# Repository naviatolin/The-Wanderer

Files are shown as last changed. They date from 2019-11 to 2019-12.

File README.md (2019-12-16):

# The-Wanderer
Principles of Engineering (POE) Final Project

Electronics-CAD has the electrical schematic using Kicad
Firmware has the Arduino and Raspberry Pi code
Computer_Vision has the computer vision code used by the main Raspi code
The_Wanderer_Website has the website code using Hugo
CAD has the mechnical design files using Solidworks

Within the Firmware folder, i2c_demo is the Raspi code and wheelrun is the Arduino code

See the video of the robot here: https://youtu.be/TBcPSCrN2iE
See the website here: http://poe.olin.edu/2019/wanderer/

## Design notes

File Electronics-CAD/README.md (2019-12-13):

Add the .lib files in this folder to Kicad
Poe_Elias.lib includes an Arduino Uno symbol from a different classmate
Raspberry_Pi_2_3.lib is from https://github.com/lukaneco/Raspberry-Pi-3-library-for-kicad but their part is not actually used.
There are other parts saved to that library folder such as Raspberry_Pi_3 that Case modified existing parts for.

Run The-Wanderer.sch in Kicad to edit the schematic.

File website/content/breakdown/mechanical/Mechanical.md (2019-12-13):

---
title: 'Mechanical Breakdown'
---

There are two main components to the mechanical design: the legs and the chassis. We chose a four-bar linkage mechanism for the legs because it gave the tottering movement we wanted without being too complicated. The leg mechanism uses one continuous rotation servo for each side, giving a total of two.

<!--more-->
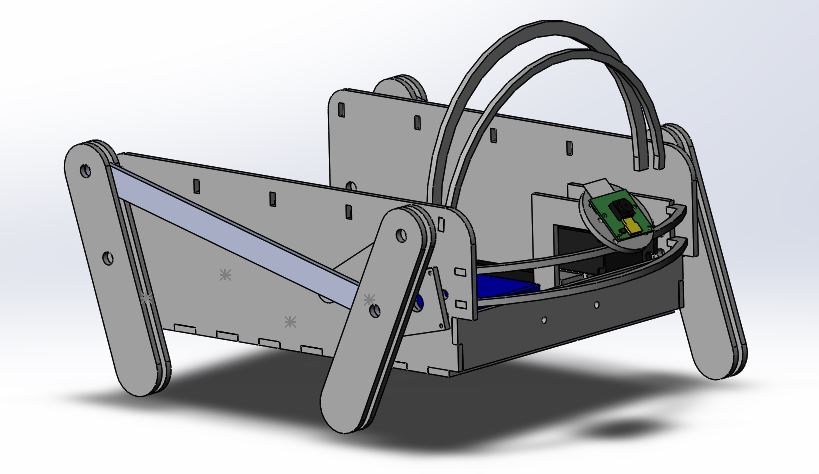
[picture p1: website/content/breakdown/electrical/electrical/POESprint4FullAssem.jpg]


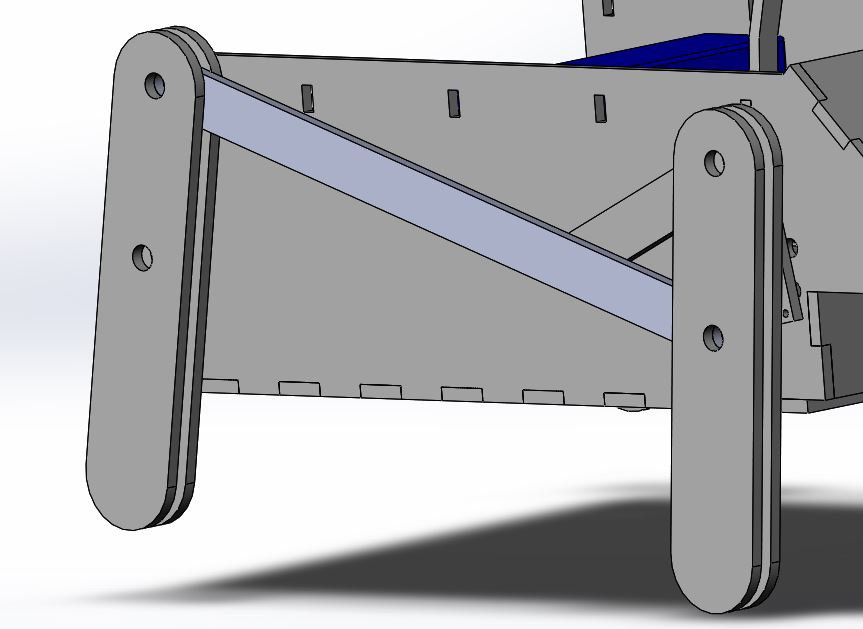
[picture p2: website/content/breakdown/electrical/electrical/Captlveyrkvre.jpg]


We used a four-bar linkage mechanism we found online ([https://grabcad.com/library/walking-robot-mechanism-1](https://grabcad.com/library/walking-robot-mechanism-1)) and adapted it to meet our design criteria. The main alterations we made to the design were scaling it up and increasing its robustness. We increased robustness by thickening the members and doubling them up where we needed more traction with the ground. We scaled up the design to fit our electronics while maintaining the size ratios between the linkages. We used the longest connector piece as our reference since it was the closest approximation to the chassis length and then scaled all the other parts of the linkage by the same factor. The legs are fabricated out of laser-cut fiberboard because it was lightweight and in abundance around our work-space.

Parallel to the mechanical design is integrating the mechanical and electrical systems together. The size of the Wanderer is mostly determined by the space needed for internal electronics and wire routing. The arrangement of the internal electronics ensures that each component can function and the software team can connect to the Raspberry Pi and Arduino for programming.

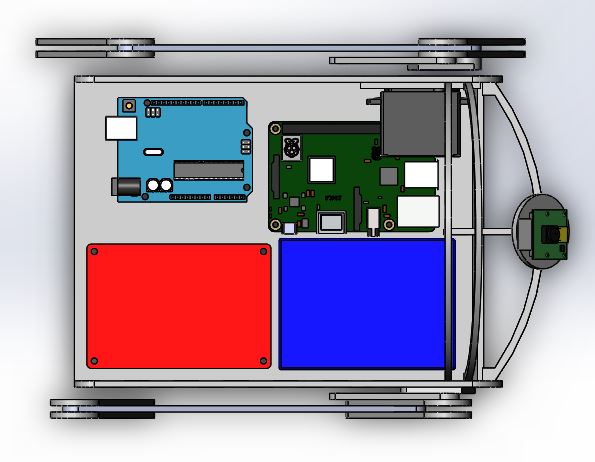
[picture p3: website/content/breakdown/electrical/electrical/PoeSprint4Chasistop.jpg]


One of the main goals of our project was to make our robot cute. One of the biggest things we did to accomplish this was the design of its motion and the use of the leg four bar linkage, Another large part was the overall aesthetic design of the chassis. One of our biggest aesthetic design features in the bright fuchsia fur we used as a skin for our robot. In order to accommodate this and improve the overall shape of the chassis, we added a set of ribs to the top of our robot: 5 uniformly spaced and one slightly smaller and tilted forward at the front, and a set of two much smaller ribs on the front. With the fur stretched over them, they gave the robot a cute animal-like shape. 

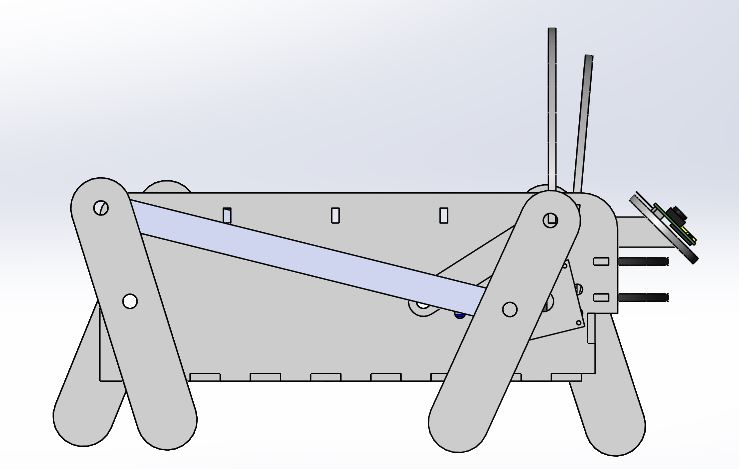
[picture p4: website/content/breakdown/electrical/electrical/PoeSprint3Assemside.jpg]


In order to maintain cuteness we also needed to disguise our sensors. We hid the camera as part of the robot's nose design. We mounted it at a 45 degree angle on a stalk that connected to the bottom of the chassis and such out of the robot just above the front ribs. We hid the IR sensor by mounting it slightly inset at the bottom of the front of the robot so that it would not be visible from above.  

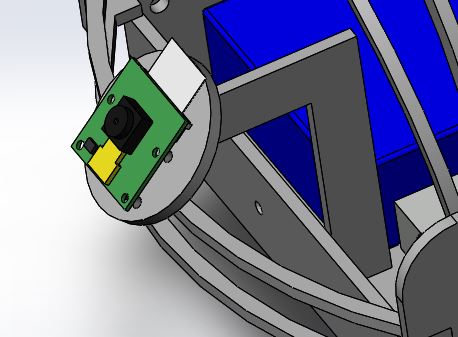
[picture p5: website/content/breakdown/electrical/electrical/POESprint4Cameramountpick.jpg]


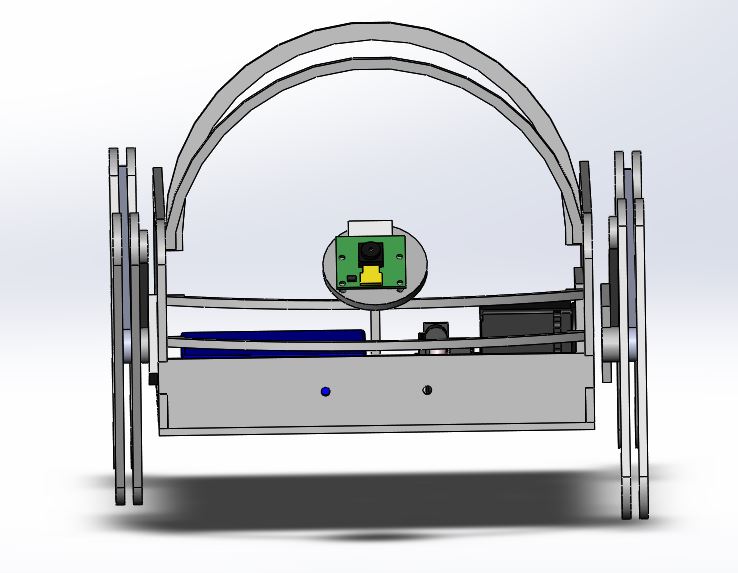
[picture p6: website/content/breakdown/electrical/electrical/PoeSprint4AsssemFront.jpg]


When it came to final assembly, the large laser-cut pieces were clamped and wood glued, then the smaller pieces were superglued. Any holes for mounting electrical components had press fit threaded inserts, allowing for easier installation than nut and bolt fastening. The leg mechanism to servo connection required one 3D printed piece, and the rest of the leg mechanism was fastened with plastic shafts and spacers.

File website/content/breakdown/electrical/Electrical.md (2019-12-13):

---
title: 'Electrical Breakdown'
---
For the electrical design, the biggest step was converting 12V battery power to 5V for the Raspberry Pi and servo motors. Two voltage dividers were needed to allow signal capture while preventing pin damage. The rest of the electrical was connecting components so that the software team has everything they need to program the robot behavior. The schematic for the electrical design is below, and subsystem descriptions follow.

<!--more-->

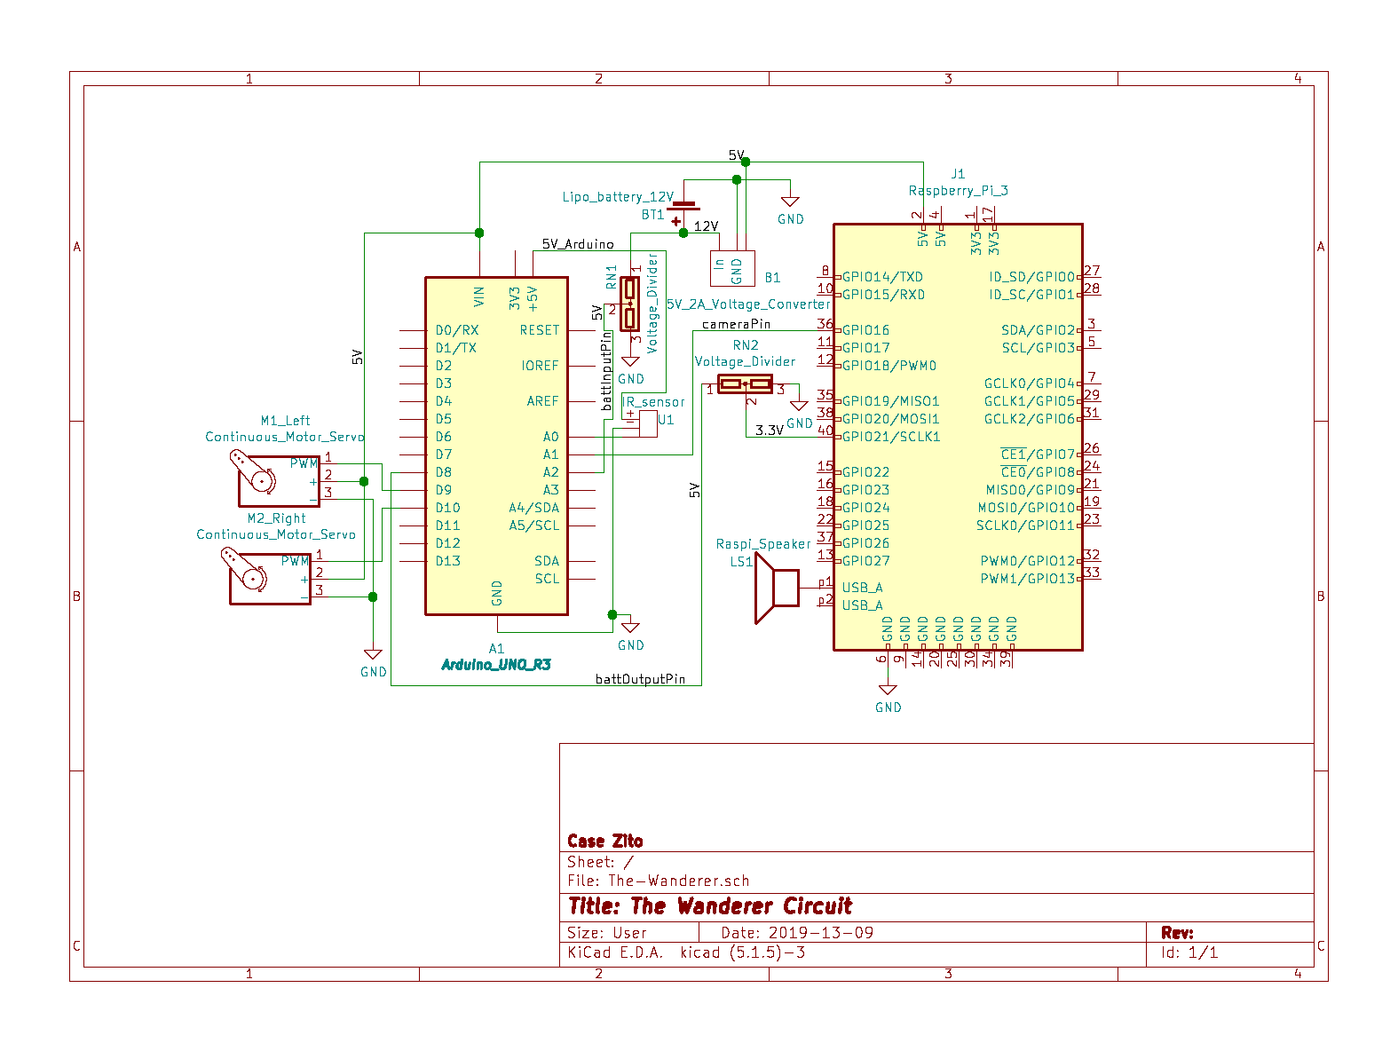
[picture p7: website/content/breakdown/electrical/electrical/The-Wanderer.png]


## Power Conversion:

- The 12V battery directly powers the Arduino while the Raspberry Pi and Servos require 5V with significant current. We used 4 5V 0.5A voltage converters in parallel to provide ample power. We chose these components because they were readily accessible and simple to implement; providing 12V and ground, these ICs output 0.5A at 5V with proper heat dissipation. We needed to supply at least 1A of current to the Raspberry Pi to keep up with sustained peak load while processing images, so we doubled the power capacity of the conversion circuit to accommodate any future components, which turned out to be the servos. A simpler thing would be to use a 5V 2A voltage converter (linked in our bill of materials).

## Voltage Dividers:

- Battery monitoring by Arduino- To prevent overdraw of the battery, we want the system to measure the level of the battery. With a range of 10.8-12.6V, the Arduino cannot natively sample the battery level, so we constructed a voltage divider with a scale factor of 0.231, placing the measured battery level in the 2.5-3.0V range. The resistor values used for this divider are 9k and 30k, where 9k/(9k+30k) = 0.231.
- Low battery signal from Arduino to Raspberry Pi- The Raspberry Pi and Arduino have differing logic levels of 5V and 3.3V, respectively. For the Arduino to indicate a low battery, its 5V digital signal must drop to 3.3V. Since this connection is only one way, we used a voltage divider with a scale factor of 0.66. The resistor values used for this were 10k and 20k, giving 10k/(10k+20k) = 0.66.

## Arduino Pins:

Arduino directly powered by the battery through the barrel jack

- A0- connected to the output of the infrared sensor
- A1- connected to the Raspi pin 36, the cameraPin
- A2- measures the battery level through a voltage divider, the battInputPin
- D8- sends the "low battery signal" to the Arduino through a voltage divider input, battOutputPin
- D9- PWM signal for the left servo motor
- D10- PWM for the right servo motor

## Raspberry Pi Pins:

Raspberry Pi powered by the 5V2A converter on pins 4 and 6.

- GPIO16 (pin 36)- sends person detection indication to Arduino (cameraPin)
- GPIO21 (pin 40)- receives low battery indication from Arduino through a voltage divider
- USB- USB speaker for sounds
- Note: In order to program the Raspberry Pi, we used a wireless mouse and keyboard and then plugged a monitor into the HDMI

## Other Components:

- The IR sensor is powered and monitored by the Arduino
- The servos are powered by the 5V2A converter and controlled by the Arduino's PWMs

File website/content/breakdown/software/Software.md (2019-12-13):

---
title: 'Software Breakdown'
---

Github: [https://github.com/naviatolin/The-Wanderer](https://github.com/naviatolin/The-Wanderer)
<!--more-->

### Communication between Raspberry Pi and Arduino

Initially, we were going to use some form of serial communication to exchange information between the Raspberry Pi and Arduino. We successfully prototyped this but eventually scrapped it in favor of simple digital pin indicators, even though this meant some extra hardware. The Raspberry Pi sends a digital signal to the Arduino to indicate the presence of a person, at which point the Arduino stops the motors. The Raspberry Pi is 3.3V logic level, so the Arduino measures this digital signal on an analog pin. In the final product, we set the Arduino to test the battery level and relay whether it is below a set level or not to the Raspberry Pi via a digital pin. 

### Arduino "Wheelrun" Code

The Arduino's main function is to control the movement of the robot. The proxPin reads analog voltage from the IR sensor and at a certain threshold the code has the robot turn (one wheel going forward, the other backward) in order to avoid obstacles. The Arduino also monitors the battery level through the battInputPin and converts the signal to a High or Low out of the battOutputPin to communicate low battery to the Raspi. From the Raspi, the cameraPin tells the Arduino to stop when the Raspi sees a person.

### Raspberry Pi "I2C_demo" Code

For part of our prototyping process, we explored having the Raspberry Pi and Arduino communicate with I2C. Although we used digital pins in the end, we did successfully exchange information between them using I2C. In I2C_demo we have the Raspberry Pi look for people through the Raspi camera, then tell the Arduino if it sees them through the pin 36. The Raspi also handles the speaker for the robot. If it receives a low battery signal from the Arduino through pin 40, it outputs a "low battery" sound. When the camera sees a person it outputs a "hello" noise and after 8 seconds, roughly the time it takes to process that a person would no longer be there, it outputs a "goodbye" noise.

### Computer Vision Code

Using OpenCV for Python, we used an implementation of the YOLO-COCO algorithm from a previous software project. This is the most computationally intense part of the project and is why we added the Raspberry Pi to the Wanderer. YOLO-COCO breaks in image down into an array of variously sized pieces (called a blob) and treats each with a large (300MB) weights file to detect a wide range of objects. To minimize computation time and increase robot responsiveness, we reduced the blob size to a minimum, sacrificing some detection ability. In the future, we would probably switch to a more specialized version of YOLO-COCO to reduce computational load.

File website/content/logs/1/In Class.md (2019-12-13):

---
Title: Oct 18, 2019
weight: 1
---
<!--more-->
## Goals

- Get started on the individual tasks that we have assigned.

## What Did We Get Done

- decided on walking mechanism - wheels for
- case: wheels running
- how the legs will incorporate
- chassis cad
- started on circuit schematic related things
- opencv testing

## Teaching team feedback

- Adding an axis of movement increases difficulty by a lot
- Having legs that move is much more difficult than wheels, so may have to go back to wheels
- Make sure the software can do what we want it to early, because if we run into issues with computer vision it will halt progress in our project
- Sensing is a difficult part, especially for connecting the sensing to the computer vision

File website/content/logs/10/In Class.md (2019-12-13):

---
Title: Nov 15, 2019
weight: 10
---
<!--more-->
## Goals

- raspi arduino communication
- put holes in the cad
- get the crank cad started
- block diagram

## What Did We Get Done

- block diagram



- we have successfully communicated whether or not we see people between the arduino and the raspberry pi
- started the crank cad
- holes in the cad

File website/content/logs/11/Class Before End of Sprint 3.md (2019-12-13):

---
Title: Nov 19, 2019
weight: 10
---
<!--more-->
## Class Before End of Sprint 3

On the mechanical side, the robot was completely assembled by Anna and Michael on Sunday. Case  uploaded the Arduino code to the robot and modified to work for the new Servo motors. One leg was not working correctly, and from Case and Michael trouble shooting it became apparent that it was a mechanical issue.

## Goals

During today's class, we focused on fixing the mechanical issues with the legs. Anna and Michael worked on adding spacers and loosening joints for the legs so they would have less friction and be able to move. Navi and Case had finished their respective parts of the code, Raspi writing to digital pins when it sees a person or is talking, and the Arduino running the motors and deciding when to stop (based on Raspi) or turn. We had the goals to upload speaker sounds to robot and to look at requirements of the website.

## What Did We Get Done

We fixed the mechanical issues and then tested the Arduino movement code. We fixed up the movement so that it successfully moves forward and turns. We also found that we will be prepared to upload to the robot because we can convert Notion pages to markdown or html. Tomorrow we will upload speaker sounds to robot.

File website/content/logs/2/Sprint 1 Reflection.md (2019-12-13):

---
Title: Oct 25, 2019
weight: 2
---
<!--more-->
## Sprint 1 Reflection

## Plusses

### Navi

- We worked really well together on gettting things done and had great communication
- Came up with clear implementation plans very quickly
- Ideated well
- We vibed

### Michael

- Mental Health transparency
- Lots of CV work ported over from SP19
- Communication
- Lots done in class
- Progress updates

### Case

- good communication
- good product, i feel accomplished
- we're sticking to our goals and routines well
- felt listened to in meetings
- got everything we wanted to done!

### Anna

- good team dynamic
- productive meetings
- good communication
- I like our project
- well scoped

## Deltas

### Case

- Did the assembly kinda last minute
- lasercutting was also a bit last minute, and if we had to make serious changes to the CAD the schedule would have gotten messed up (do earlier separate CAD? have a more set idea of things early? idk)
- not always sure what's happening with subtasks before i ask- clear progress checks about specific tasks is good moving forward into more complicated things
- uneven writing and tracking of tasks (team captain for a meeting)
- presentation was a little rocky, practice more

### Navi

- documentation and website/blog as this is our final deliverable
    - i could've done a better job as a pm
- need to set up clear tasks and objects every meeting - need to spend 10 minutes just doing stuff like this
- could've practiced presentation
- could've done another iteration as well?
- could've talked more about the personality as a group and had an ideation session
- next sprint should meet more outside of class

### Michael

- Improve aesthetics of robot for sprint 2
- Presentation practice
- Use github more
- Gimme more tasks!

### Anna

- not enough meetings
- Practice presentation/ evenly divide slides
- more involved schedule
- get my cad in github

## Next Sprint

Kaizen: More meetings and more documentation (be more thorough)

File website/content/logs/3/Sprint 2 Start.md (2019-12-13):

---
Title: Oct 27, 2019
weight: 3
---
<!--more-->
## Sprint 2 Start

## Goals

- Assigning tasks for sprint
- Making a sprint calendar
- knowing sprint goals
- start working on sprint tasks
- talk about personality and do some ideation

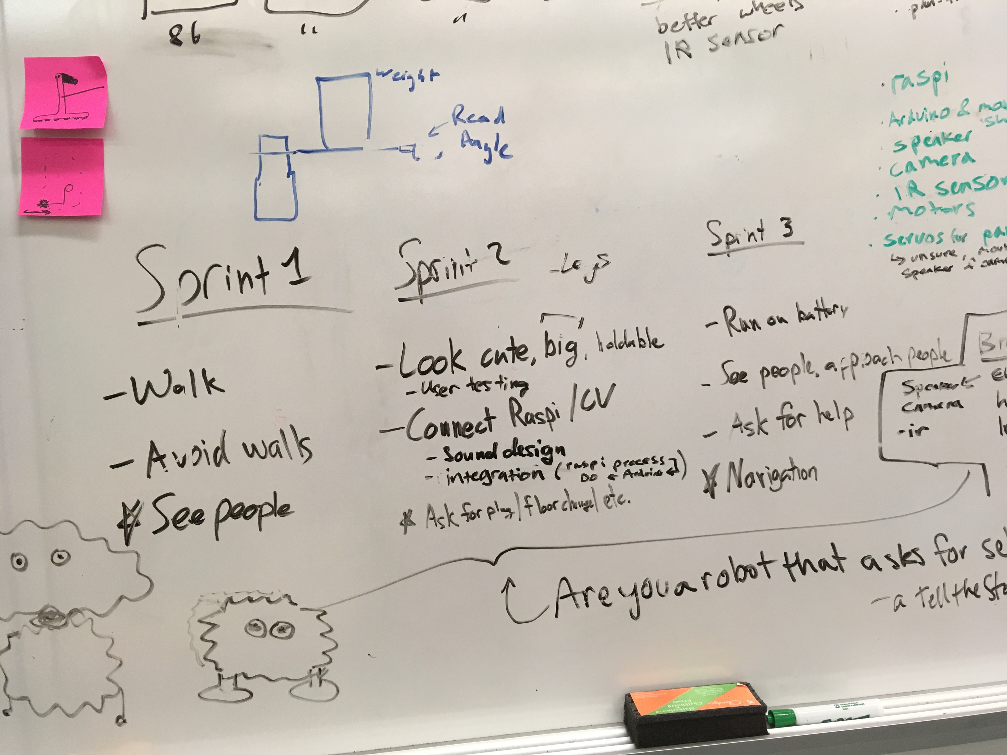
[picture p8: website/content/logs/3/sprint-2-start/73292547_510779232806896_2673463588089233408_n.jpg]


## What Did We Get Done

- we got sprint 1 finished

## Reflection (Where could we improve in the future?)

We decided sprint priorities, scheduled our sprint tasks, and then focused on personality/aesthetic ideation

We want to track time we spend on tasks for sprints

We decided team bonding

we decided on immediate tasks

We were not able to start sprint tasks much

## Priorities for Sprint

- Good mobility → turning, walk forward
- Chassis fits all components, decide all components will be on all of it
- Figure out sensor requirements, what components we will have
    - We decided to do minimum sensors for now, and scale up if needed. This means the head will just have one servo
    - Two DC motors for legs, one IR sensor, Raspi camera, Raspi speaker, Arduino & motor shield, Raspi, servo for head tilt
- Raspi and Arduino communication, proof of concept that we can send commands to Arduino
- Personality/design goals → decide what inspiration we want for design and what thing we want to

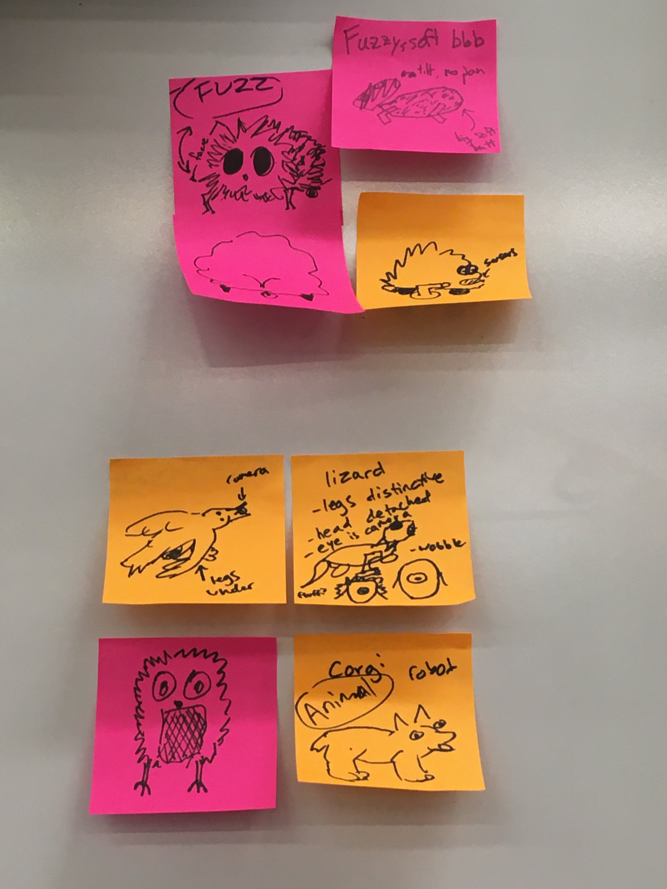
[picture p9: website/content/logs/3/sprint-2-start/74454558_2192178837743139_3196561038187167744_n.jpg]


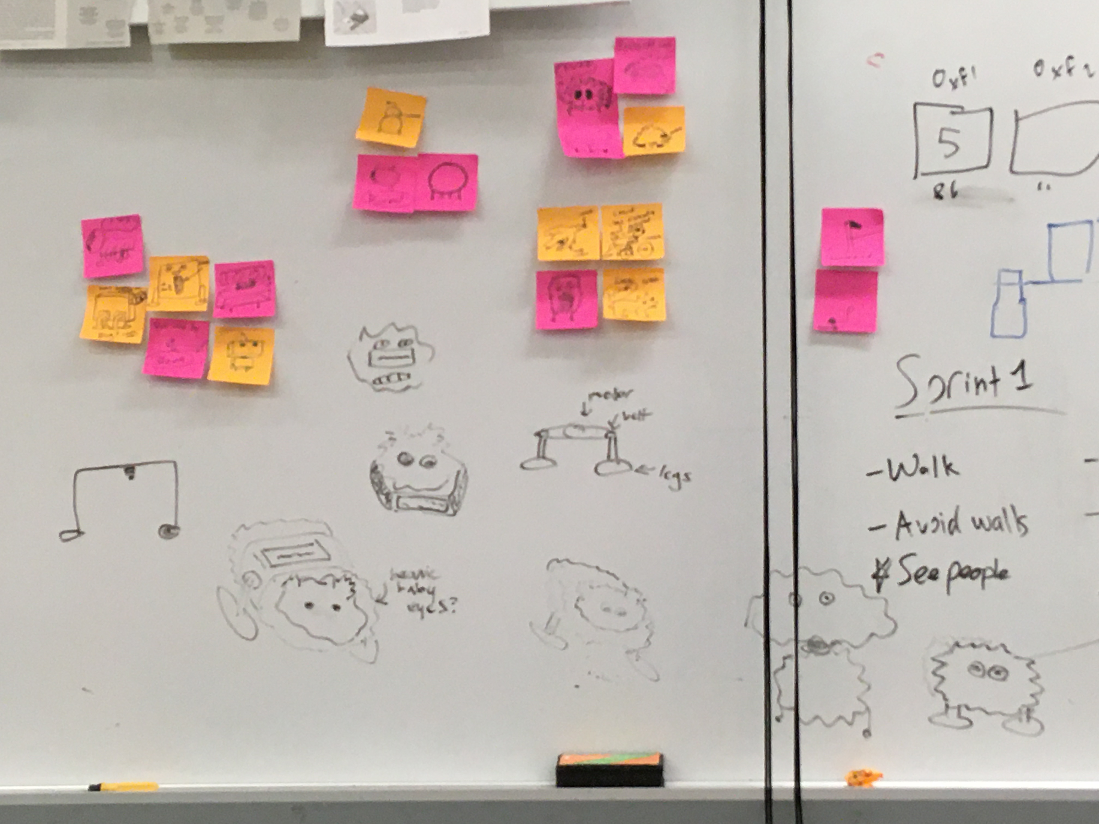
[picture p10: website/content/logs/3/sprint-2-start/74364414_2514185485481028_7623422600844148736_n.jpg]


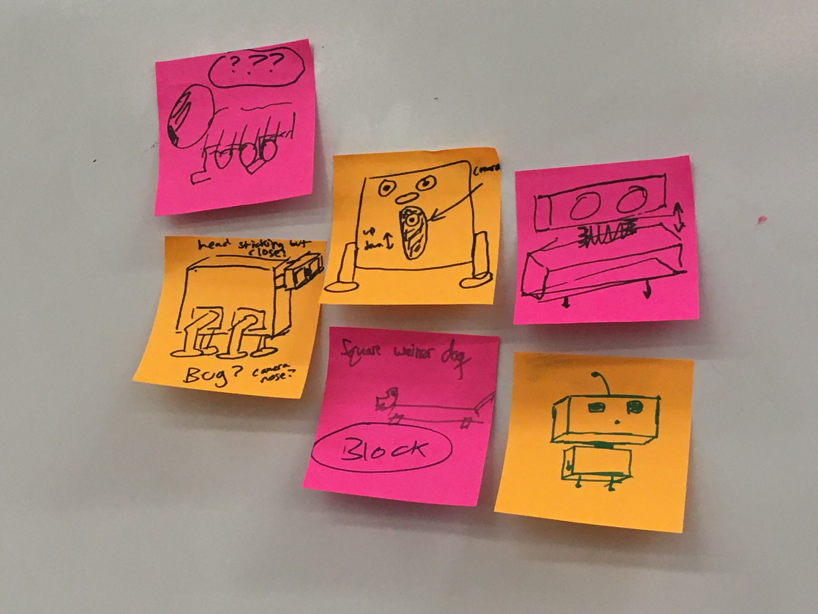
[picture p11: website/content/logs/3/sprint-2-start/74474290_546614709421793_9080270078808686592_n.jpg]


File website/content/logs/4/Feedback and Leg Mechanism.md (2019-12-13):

---
title: Oct 29, 2019
weight: 4
---
<!--more-->
## Feedback and Leg Mechanism

## Goals

- Figure out our feedback
- Finalize the leg mechanism

## What Did We Get Done

- Got the raspberry pi partially set up (getting python 3 and open cv stuff on it)
- stared at leg mechanism
- made progress
- started on getting the website up

## Reflection (Where could we improve in the future?)

- walk into the meeting with clearer goals and realistically estimate the deadlines

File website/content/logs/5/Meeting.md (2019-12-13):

---
title: Nov 01, 2019
weight: 5
---
<!--more-->
## Goals

- Decide what we want for our team bonding
- Tonight: Have dinner, have fun

## What Did We Get Done

- Anna researched wheels
- Navi got first pages of github website showing
- We ran into an error where the raspberry pi crashed every time we tried to run the python code to detect people. We then tried to use Simple CV and other example people got working on their 1GB ram raspberry pis. The raspi continued to crash. :(

## Reflection (Where could we improve in the future?)

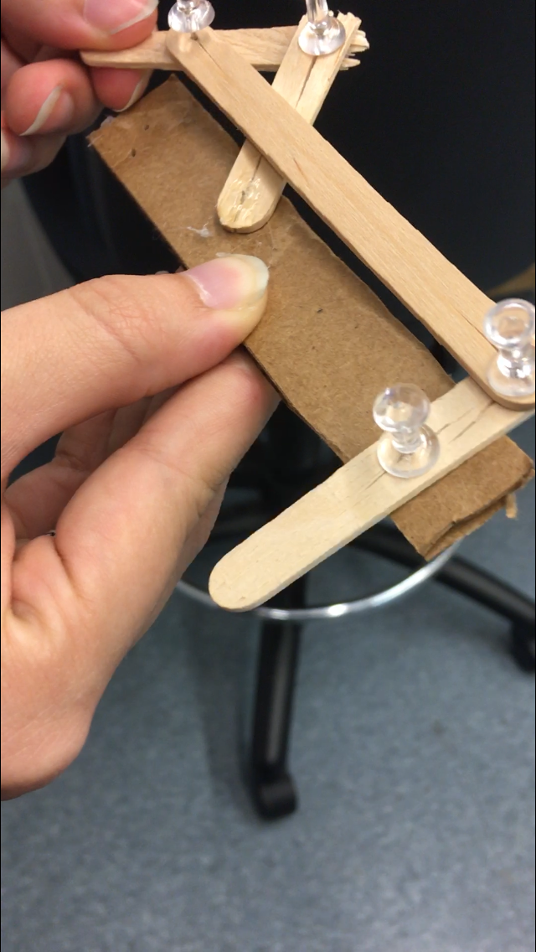
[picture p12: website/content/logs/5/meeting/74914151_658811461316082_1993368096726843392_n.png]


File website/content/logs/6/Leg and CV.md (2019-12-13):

---
Title: Nov 03, 2019
weight: 6
---
<!--more-->
## Leg and CV!

## Goals

- Figure out the rest of the CV situation
- Figure out the chassis and leg situation

## What Did We Get Done

- We fixed the issue with the CV crashing the raspberry pi. We realized that this was due to a power supply issue where the previous brick was only supplying the raspi with 0.7A of current where we really actually needed 2.5 to 3 A of current. This was a big win. We now have proof of concept that the raspberry pi can detect people in it's field of vision.
- With the legs, we finished cadding them and decided on what the chassis would look like for this sprint.
- Yesterday, we went to the thrift store and bought potential skins.



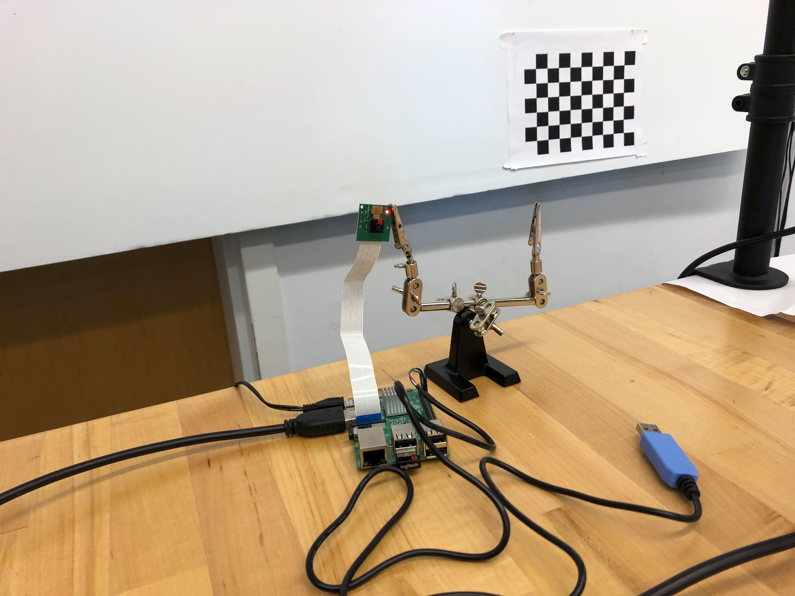
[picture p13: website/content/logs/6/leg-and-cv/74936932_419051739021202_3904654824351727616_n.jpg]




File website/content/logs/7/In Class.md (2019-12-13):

---
Title: Nov 05, 2019
weight: 7
---
<!--more-->
## Goals

- Construct the prototype from lasercut pieces
- Start working on different skins

## What Did We Get Done

- We got the Raspberry pi and the arduino to communication using i2c. The arduino blinks based on information sent to it using the raspi.



- We got some skins for the robot using the children's clothing we thrifted earlier.
- Cadded spacers, made edits to the chassis
- Laser cutting out a box for the chassis as a skin
- next revision will be putting this power supply on a piece of metal
- need a thing that will shut off the robot if the power is overdrawn
- 2 amp 12 v to 5 v converter - the raspberry pi only taked 5v but the arduino can handle 12 but will step it down to 5 volts



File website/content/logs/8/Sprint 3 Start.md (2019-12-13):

---
Title: Nov 10, 2019
weight: 8
---
<!--more-->
## Sprint 3 Start

## Goals

- Look at slide feedback and reflect
- Look at sprint goals and create tasks for the sprint
- decide what things we will buy this week
- Test out prototype and see how it moves
- Integration mechanical goal: making working chassis
- Mechanical mechanical goal: increasing stability of legs, 3D print attachment, order better motors
- Software goals: comp vis to moving something, get speakers to work, get LCD working
- Figure out how to integrate more as a team

## What Did We Get Done

- Set goals for sprint
- planed out tasks for sprint
- decided things to order
- split up tasks for software and made smaller due dates

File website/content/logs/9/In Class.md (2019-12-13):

---
Title: Nov 12, 2019
weight: 9
---
<!--more-->
## Goals

- Mechanical: decide on a chassis design, get cadding
- chat with aaron about stability and weights
- finish figuring out raspi arduino stuff
- brainstorm and try different code

## What Did We Get Done

- Case&Navi: Looked at digital IO on Raspi, played with camera angles (45deg is best), block diagrams/state machine of robot behavior
- Anna & Michael: Sketched out chassis stuff, talked about motor power and structure stability, walks with weights
- Michael: Ordered perfboard for the circuit
- Order sheet: IR sensor, speaker, motor, battery

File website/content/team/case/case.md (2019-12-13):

---
title: 'Caze Zito (He/Them)'
---
<!--more-->
{{< figure src="case.jpg" width="400px">}}

Case is a electrical and computing engineer who also often does software. They really loved doing a lot of Arduino coding for this project, circuit schematic making, and other bits and pieces for this project. It was great to see the fluffy monster that came out of everything.

Github: [https://github.com/CaseZito](https://github.com/CaseZito)

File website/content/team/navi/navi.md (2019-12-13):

---
title: 'Navi Boyalakuntla (She/Her)'
---
<!--more-->
{{< figure src="navi.png" width="400px">}}

Navi is an product design engineer (EECS with Design) at Olin College of Engineering. She enjoyed working on integration between the arduino and the raspberry pi and working on developing the robot's personality. She also took on the role of project manager in this team using tools like agile scrum and Notion.

Github: [https://github.com/naviatolin](https://github.com/naviatolin)

LinkedIn: [https://www.linkedin.com/in/pranavi---boyalakuntla/](https://www.linkedin.com/in/pranavi---boyalakuntla/)

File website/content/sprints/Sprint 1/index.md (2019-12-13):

---
title: 'Sprint 1'
---

## Goals:

- Make a robot that walks around and can sense walls
- Show proof-of-concept for components
    - Computer vision demonstration
    - Walking mechanism

## Progress:

- Robot walks and can sense walls. It is able to turn before the wall
    - Computer vision can recognize people
    - Basic walking mechanism
<!--more-->
## Mechanical

- Create a rectangular chassis to mount motors, wheels, IR sensor, and Arduino
    - There are three wheels, one on front two on back
    - Moves forward with 2 legs driven by motors. The legs spin around with the foot facing downward, dragging it forward
    - Mount IR sensor on the front to sense walls

{{< figure src="sprint1pic1.jpg" width="400px">}}
{{< figure src="first_proto.png" width="400px">}}

## Software

- Code that turns robot before wall, and runs legs

## Design

- Robot wobbles and walks slowly

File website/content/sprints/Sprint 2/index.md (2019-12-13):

---
title: 'Sprint 2'
---
We want to develop the personality of the robot more especially with mechanical design and do a lot of user testing to make sure that the robot is "cute" and personable.

## Goals:
- Implement computer vision on the Raspberry Pi
- Use Raspberry Pi to communicate with Arduino
- Improve walking mechanism
- Develop robot appearance/personality especially making it "cute"

## Progress:
- Moves with improved linkage leg mechanism
- Can identify people with the Raspi camera
- Has fluffy "pink monster" appearance people found cute
- The walking mechanism has a wobble aspect which adds a cute personality factor
- Arduino LED lights up when Raspi sees a person (10 sec)

<!--more-->

## Mechanical

- Have a functional leg mechanism
    - iterations: foot shape, 3D print, longer legs
    - [https://grabcad.com/library/walking-robot-mechanism-1](https://grabcad.com/library/walking-robot-mechanism-1) Decided on 4 leg linkage design based on this

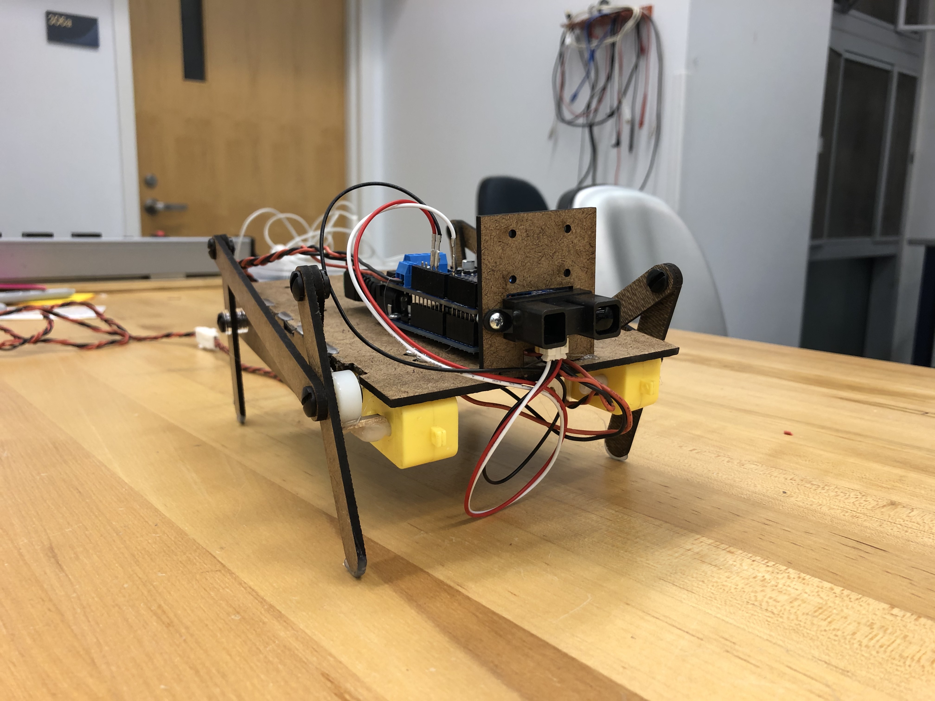
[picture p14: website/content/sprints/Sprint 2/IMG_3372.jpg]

Markdown Monster icon

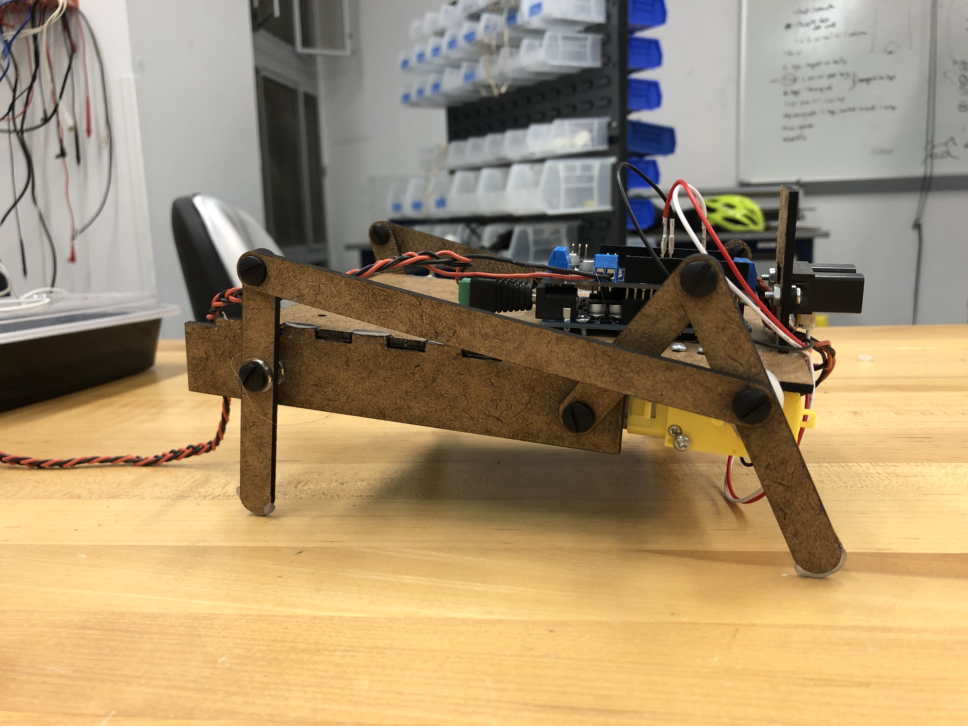
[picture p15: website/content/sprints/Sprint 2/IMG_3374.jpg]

Markdown Monster icon

## Software

- Finalize sensors we want and goals
- Raspberry Pi-Arduino integration

## Design

- Research into types of walk cycles: peppy, confident, meandering, off-balance. We liked the back and forth movement that the linkage produced
- Mock up type of skins. People loved the pink fluff monster skin
    - Furry monster like (pink fluff)
    - Furry animal like (cow print fuzzy)
    - Technical look (see through panel acrylic)
- Discussed type of shape
    - Give it a butt, stuffed look
    - Make it rounder- skin sags in the middle

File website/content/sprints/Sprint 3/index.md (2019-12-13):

---
title: 'Sprint 3'
---
## Goals

- Integrate mechanical electrical and software systems
- Scale up to final size
- Increase mechanical robustness (no hot glue!)
- Run on battery power

## Progress:
- Attached new motor servos
- Added battery and convert its power for other components
- Arduino and Raspi wired to each other on chassis and communicate back and forth, with Arduino controlling movement and the Raspi monitoring computer vision and using the speaker
- Stronger larger design that is wood glued, not hot glued
- Added ribs on chassis over electronics to give round shape to body and fur

<!--more-->

## Mechanical

- Improve walking, by making legs thicker, making a CAD assembly, 3D printing crank part (so its a stronger and spaced right)

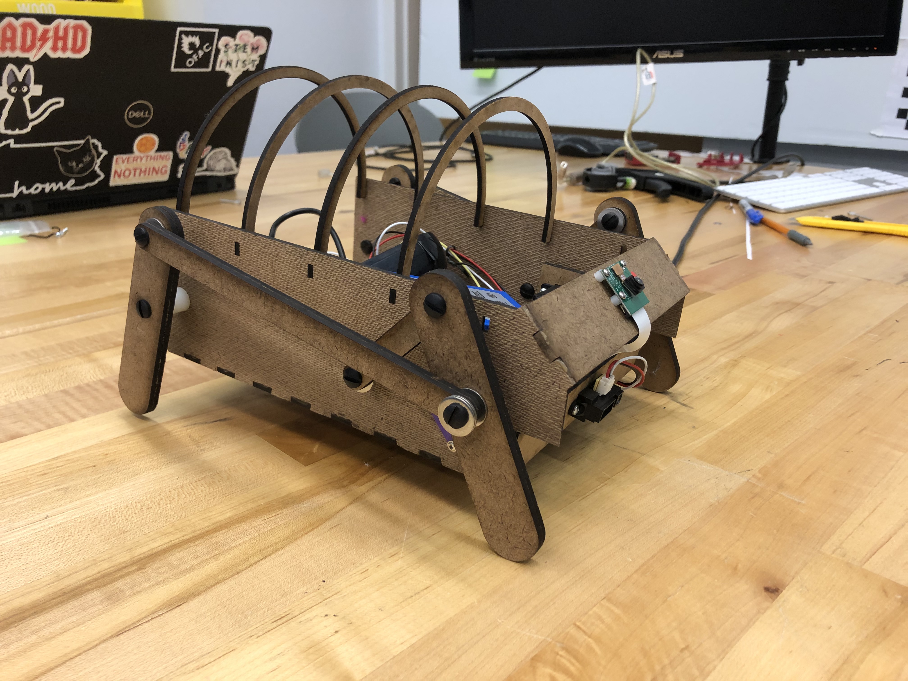
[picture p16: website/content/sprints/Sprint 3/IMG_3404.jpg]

Markdown Monster icon

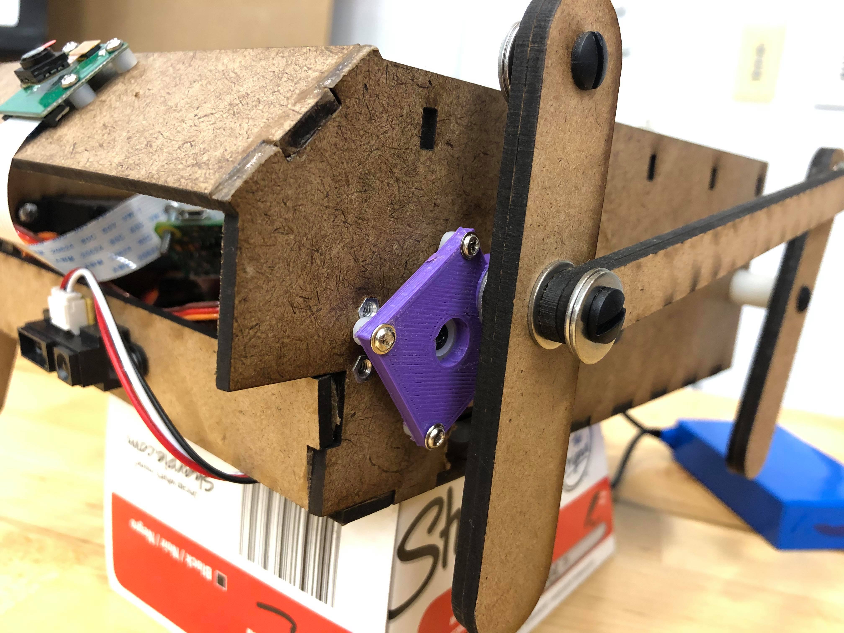
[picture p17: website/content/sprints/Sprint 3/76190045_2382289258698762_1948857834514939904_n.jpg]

Markdown Monster icon

## Electrical

- Move to battery power
- Wiring to connect Raspi, Arduino, battery, and components

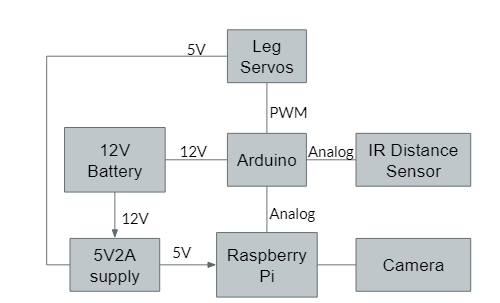
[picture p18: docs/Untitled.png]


## Software

- Add sounds, and change in movement to program interactive behavior
- Add lines of code to .bashrc Raspi file, so that the Raspi runs the computer vision/main code from start-up
- Connect Raspi GPIO pins to Arduino to communicate the "stop" signal when Raspi sees a person and is talking. Arduino should stop moving.

Markdown Monster icon

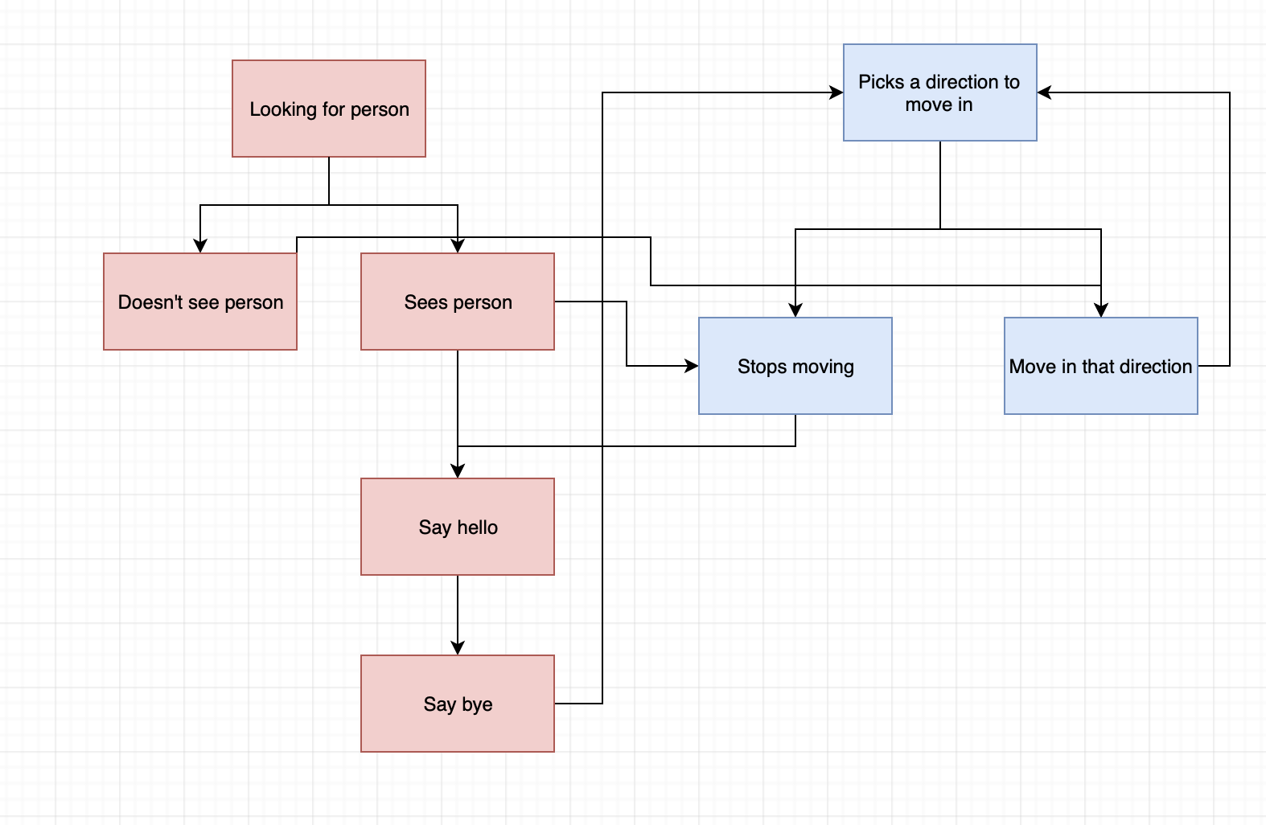
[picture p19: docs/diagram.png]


- Get speaker working and saying one sound (a roar) when it sees a person

## Design

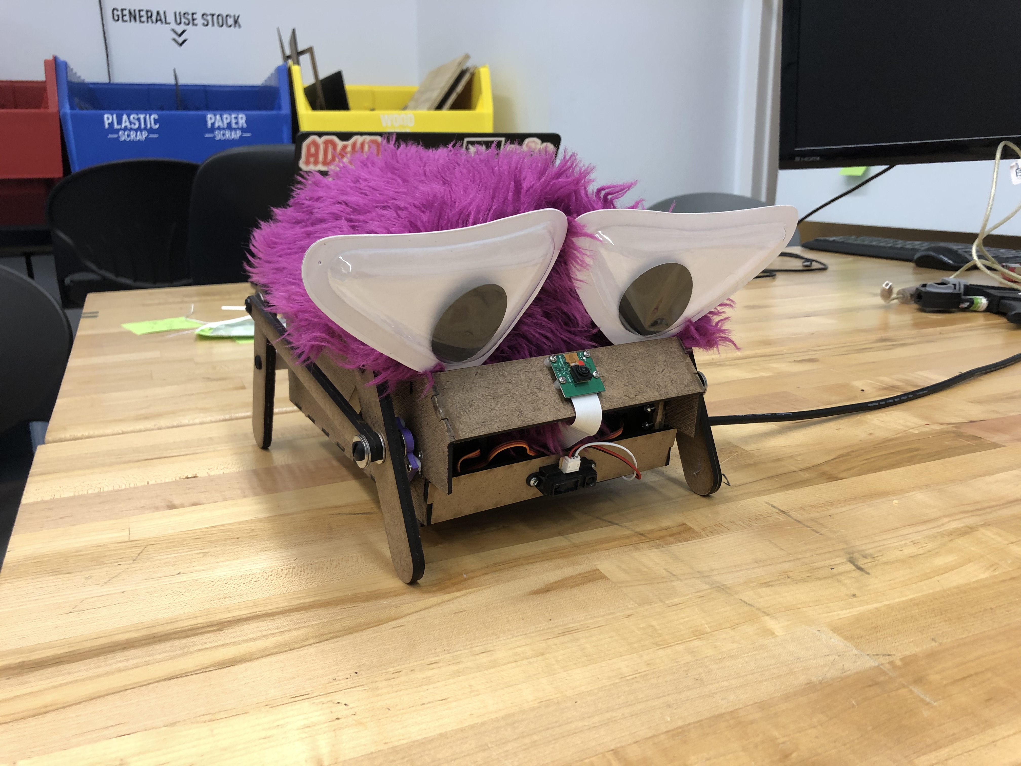
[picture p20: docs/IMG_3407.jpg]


- Iterate on appearance, creating round hardboard ribs to put fur over parts, putting on fur, putting on eyes, making it more chunky (more towards square wall-e and round ideas)

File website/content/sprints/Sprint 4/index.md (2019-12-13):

---
title: 'Sprint 4'
---
## Goals:

- Add low battery notification (over speaker)
- Redesign chassis to organize electronics for better access
- Make shape rounder
- Documentation
- Modify sounds to be more cute

## Progress:

- Added low battery notification sound by having the Arduino sense voltage from Battery, output digital high or low, convert that voltage to 3.3V range for Raspi, and have Raspi output battery low sound
- Added more small ribs to structure give a gradual rounding shape
- Redesigned chassis and had threaded inserts for parts so they held better
- Decided against modified sounds because we liked the attitude of them (very attention getting)
- Finished up Documentation
<!--more-->
## Mechanical

- Redesign chassis so that components are easier to access
- Chassis has round, semi-circle design, with ribs in the front instead of hardboard to add a round face
- Create a hardboard protrusion with a circle to come out of the fur as a fake "nose" that has the camera

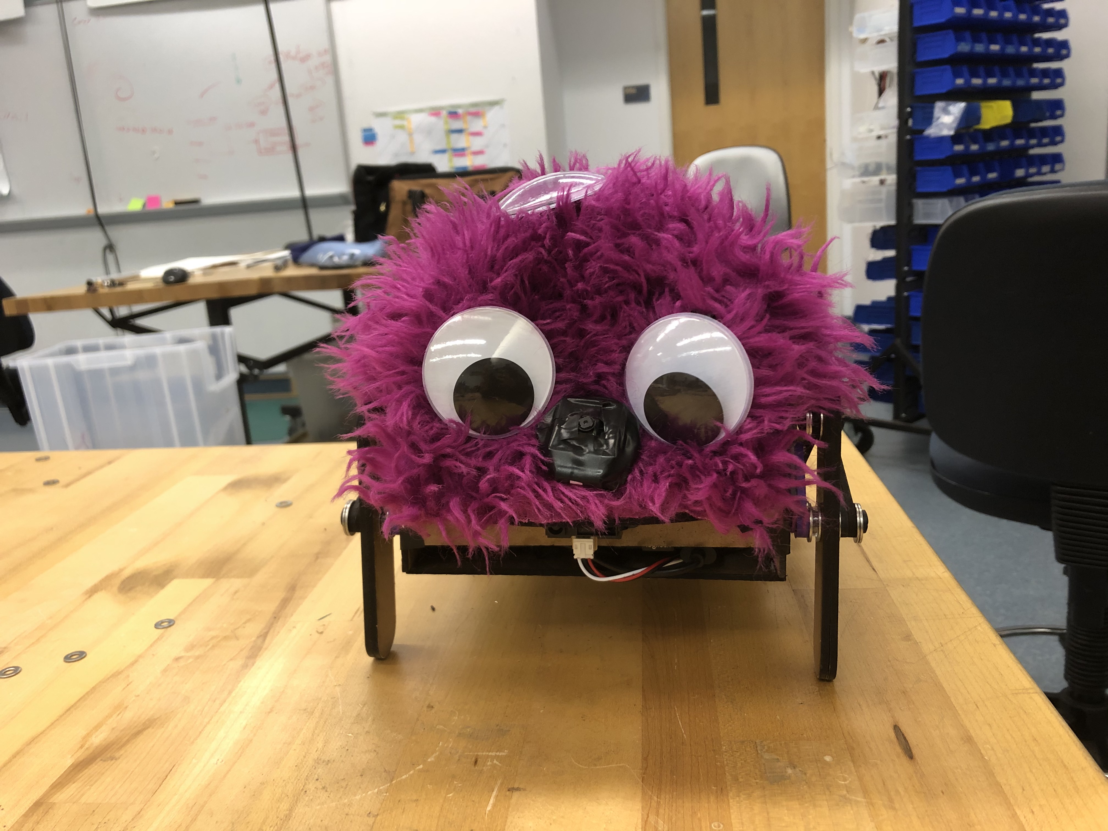
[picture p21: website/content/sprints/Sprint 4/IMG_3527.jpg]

Markdown Monster icon

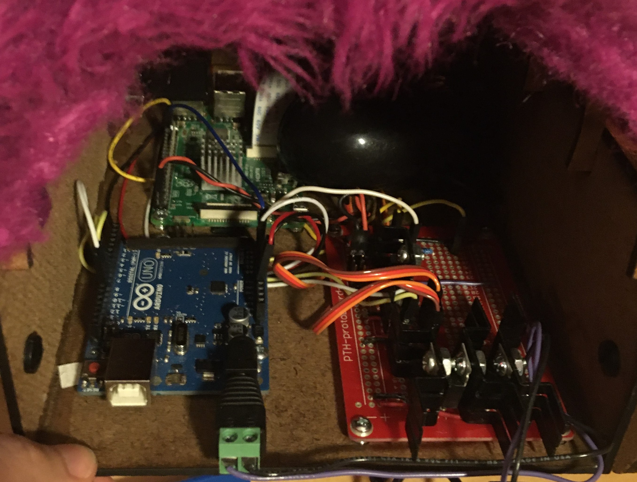
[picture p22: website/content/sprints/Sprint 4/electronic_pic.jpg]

Markdown Monster icon

## Electrical

- Create a voltage divider with a factor of 4.54 to scale down 5V output of Arduino low battery signal to 3.3V for the Raspi
- Create an updated circuit schematic

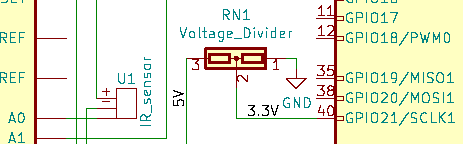
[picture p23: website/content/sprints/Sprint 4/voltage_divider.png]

Markdown Monster icon

## Software

- Add variables to Arduino and Raspi to handle reading and communication of battery

## Design

- Order new googly eyes and placed them to give a fun monster vibe
- Tape the nose to mask the camera and cover the hardboard so it's a simple black nose

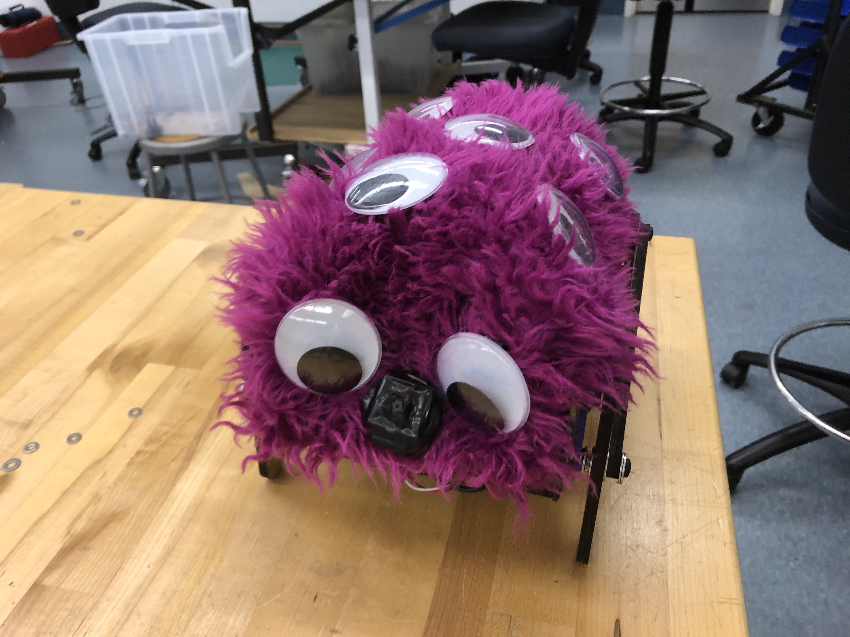
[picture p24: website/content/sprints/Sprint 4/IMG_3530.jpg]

Markdown Monster icon

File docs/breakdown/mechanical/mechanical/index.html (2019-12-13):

- Home
- BeepBoop
- Breakdown
- Sprints
- BOM
- Logs
- Team

 (https://naviatolin.github.io/The-Wanderer/)

 (https://naviatolin.github.io/The-Wanderer/)

- Home
- BeepBoop
- Breakdown
- Sprints
- BOM
- Logs
- Team

#### Breakdown

- Electrical Breakdown (https://naviatolin.github.io/The-Wanderer/breakdown/electrical/electrical/)
- Mechanical Breakdown (https://naviatolin.github.io/The-Wanderer/breakdown/mechanical/mechanical/)
- Software Breakdown (https://naviatolin.github.io/The-Wanderer/breakdown/software/software/)

# Mechanical Breakdown

There are two main components to the mechanical design: the legs and the chassis. We chose a four-bar linkage mechanism for the legs because it gave the tottering movement we wanted without being too complicated. The leg mechanism uses one continuous rotation servo for each side, giving a total of two.





We used a four-bar linkage mechanism we found online (https://grabcad.com/library/walking-robot-mechanism-1) and adapted it to meet our design criteria. The main alterations we made to the design were scaling it up and increasing its robustness. We increased robustness by thickening the members and doubling them up where we needed more traction with the ground. We scaled up the design to fit our electronics while maintaining the size ratios between the linkages. We used the longest connector piece as our reference since it was the closest approximation to the chassis length and then scaled all the other parts of the linkage by the same factor. The legs are fabricated out of laser-cut fiberboard because it was lightweight and in abundance around our work-space.

Parallel to the mechanical design is integrating the mechanical and electrical systems together. The size of the Wanderer is mostly determined by the space needed for internal electronics and wire routing. The arrangement of the internal electronics ensures that each component can function and the software team can connect to the Raspberry Pi and Arduino for programming.



One of the main goals of our project was to make our robot cute. One of the biggest things we did to accomplish this was the design of its motion and the use of the leg four bar linkage, Another large part was the overall aesthetic design of the chassis. One of our biggest aesthetic design features in the bright fuchsia fur we used as a skin for our robot. In order to accommodate this and improve the overall shape of the chassis, we added a set of ribs to the top of our robot: 5 uniformly spaced and one slightly smaller and tilted forward at the front, and a set of two much smaller ribs on the front. With the fur stretched over them, they gave the robot a cute animal-like shape.



In order to maintain cuteness we also needed to disguise our sensors. We hid the camera as part of the robot's nose design. We mounted it at a 45 degree angle on a stalk that connected to the bottom of the chassis and such out of the robot just above the front ribs. We hid the IR sensor by mounting it slightly inset at the bottom of the front of the robot so that it would not be visible from above.





When it came to final assembly, the large laser-cut pieces were clamped and wood glued, then the smaller pieces were superglued. Any holes for mounting electrical components had press fit threaded inserts, allowing for easier installation than nut and bolt fastening. The leg mechanism to servo connection required one 3D printed piece, and the rest of the leg mechanism was fastened with plastic shafts and spacers.

- www.zerostatic.io

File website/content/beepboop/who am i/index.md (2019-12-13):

---
title: 'Who Am I'
---

asdf
Markdown Monster icon

## Hello Friend! 
I am the wanderer - Olin College's very own wandering robot. I walk through the Academic Center and interact with people I see to make their days better! I won't always see you, but when I do I say hello, let you pet me, and continue on with my day. If my battery is low, as I am a robot, I will definitely let you know so you can help me out!

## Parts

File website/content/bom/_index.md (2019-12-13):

---
title: 'BOM'
date: 2018-11-28T15:14:39+10:00
---
The materials we used, how much they cost, and whether or not we had to pay for them.

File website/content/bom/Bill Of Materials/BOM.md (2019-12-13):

---
title: 'Bill of Materials'
---
Total Including Free Items: $193.08

Total Excluding Free Items: $88.08
<!--more-->
| Object | Unit Price | Owned Prior Or Made In House | Amount Used | For What | Total Price |
|---|---|---|---|---|---|
| Raspberry PI | $40.00 | Yes | 1 | Computer Vision | $40.00 |
| Camera for RasPi | $8.79 | No | 1 | Raspi Computer Vision | $8.79 |
| Servo Motors | $11.95 | No | 2 | Movement | $23.90 |
| Speaker | $12.50 | No | 1 | Raspi Sounds | $12.50 |
| Proximity Sensor (Adafruit) | $14.95 | No | 1 | Arduino obstacle detection | $14.95 |
| 12V Lipo Battery | $22.99 | No | 1 | System Power | $22.99 |
| microSD card | $5.00 | Yes | 1 | Raspi Storage | $5.00 |
| Hardboard | $30.00 | Yes | | Mechanical prototyping | $30.00 |
| Arduino Uno | $22.00 | Yes | 1 | Motion Control | $22.00 |
| ProtoBoard | $4.95 | No | 1 | Electrical Prototyping | $4.95 |
| Voltage Converter (5V 2A) | $8.00 | Yes | 1 | Supply Correct Voltages | $8.00 |

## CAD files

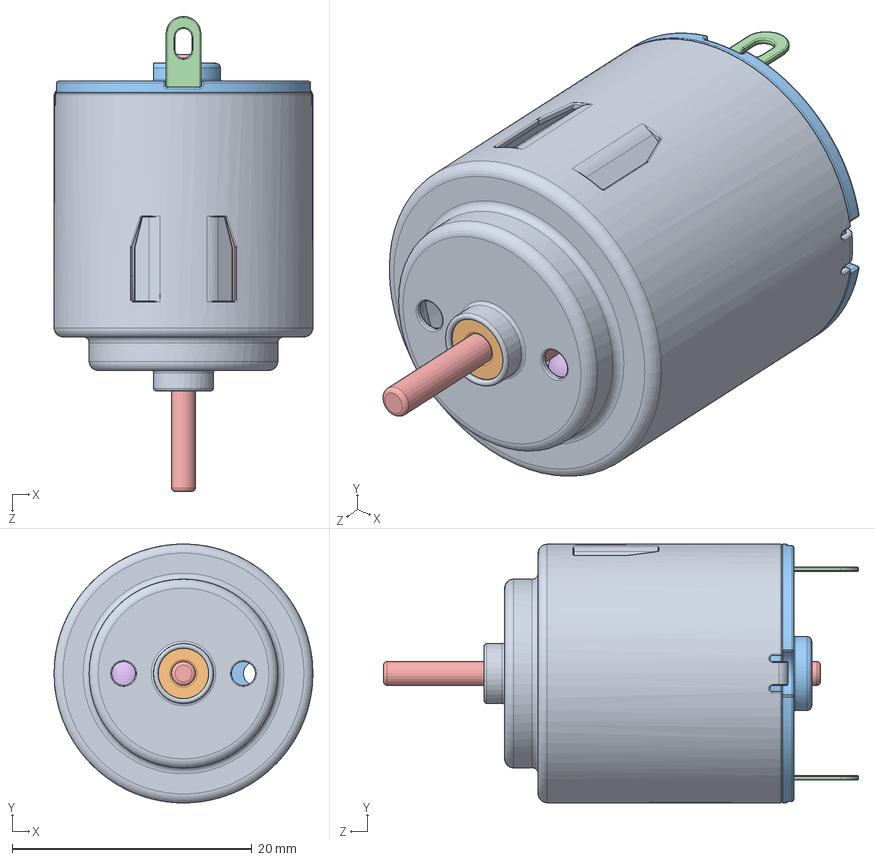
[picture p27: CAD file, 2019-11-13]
CAD/Sprint2/walking-robot-mechanism-1.snapshot.3/ELENCO DC Motor 3V.SLDASM
21.6 x 21.6 x 39.6 mm
ELENCO MOTOR HOUSING 01
ELENCO FRONT BUSHING
ELENCO MOTOR BACK 01
Terminal3V x 2
ELENCO ARMATURE 01
Enrolamento3V x 3

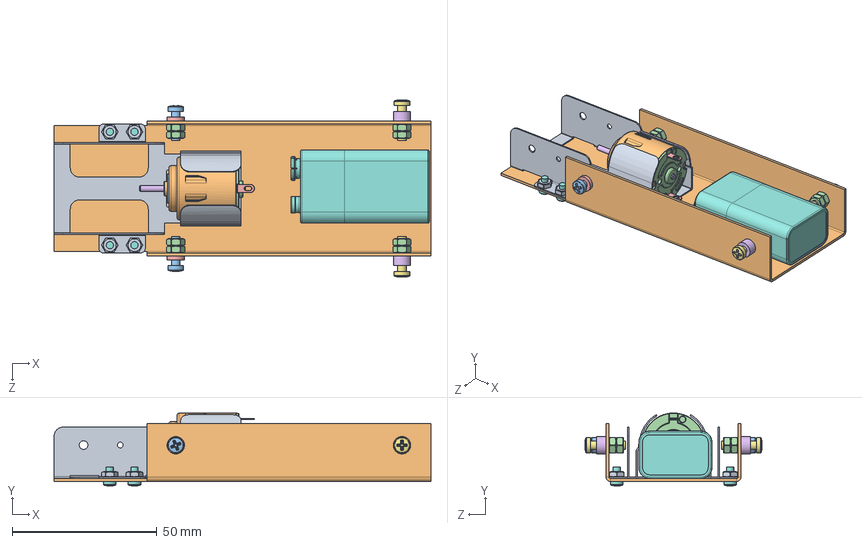
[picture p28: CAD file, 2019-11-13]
CAD/Sprint2/walking-robot-mechanism-1.snapshot.3/Walking_robot_(fixed_body).SLDASM
130.0 x 25.2 x 61.2 mm
ELENCO GEAR BOX 01
ELENCO MOTOR HOUSING 01
ELENCO FRONT BUSHING
ELENCO MOTOR BACK 01
Terminal3V x 2
ELENCO ARMATURE 01
Enrolamento3V x 3
Walking_robot_(bolt_2_5x5) x 4
Walking_robot_(nut_2_5) x 4
Walking_robot_(main_body)
Walking_robot_(bolt_3x10) x 2
Walking_robot_(nut_3) x 8
Walking_robot_(spacer1) x 2
Walking_robot_(spacer2) x 2
Walking_robot_(bolt_3x12) x 2
PR2007 9 Volt Battery

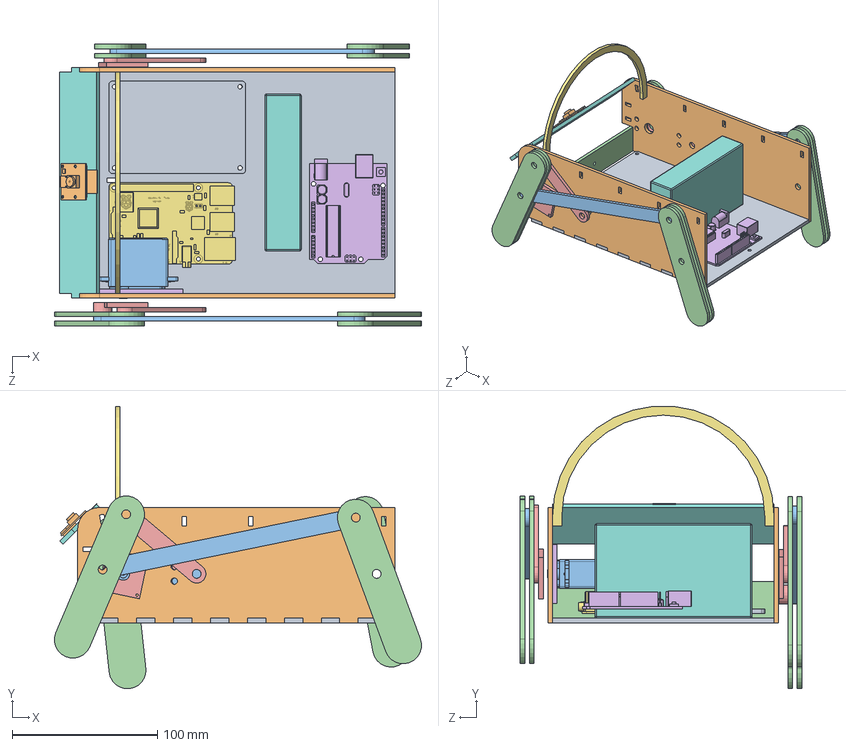
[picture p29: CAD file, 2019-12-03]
CAD/Sprint3/PoeSprint3Assem.SLDASM
252.5 x 194.2 x 193.7 mm
PoeSprint4ChasisBotom
PoeSprint4ChasisSide x 2
PoeSprint3LL x 2
PoeSprint3ML x 8
PoeSprint3SL x 2
arduino
Rpi3Bplus
Battery
PowerCircuit
RPi cam Rev 1.3
FeeTech FS5109M Metal Gear Servo Outer volume
PoeSprint3IrSensorMount
PoeSprint3Crank x 2
PoeSprint3ServoMount
PoeSprint3Rib
PoeSprint3CameraMount

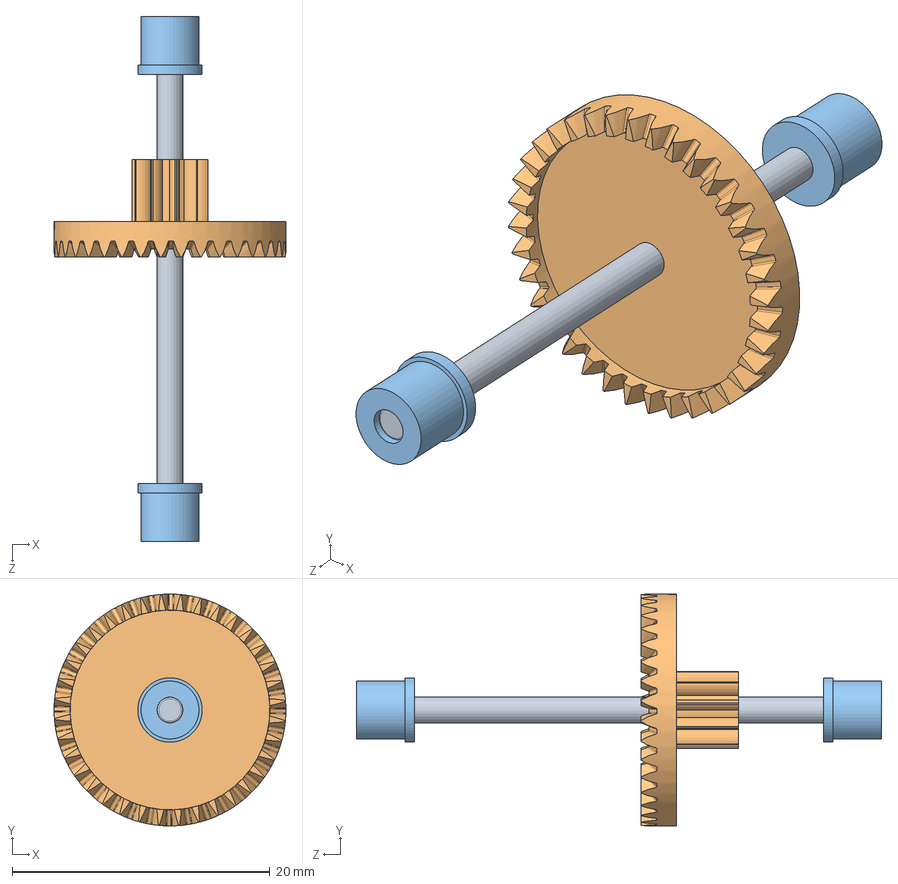
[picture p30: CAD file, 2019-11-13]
CAD/Sprint2/walking-robot-mechanism-1.snapshot.3/Walking_robot_(assembled_first_axle).SLDASM
18.0 x 18.0 x 40.8 mm
SHAFT 2 X 40
pCROWN GEAR 36T X 10T R01
ELENCO COLLAR 01 x 2

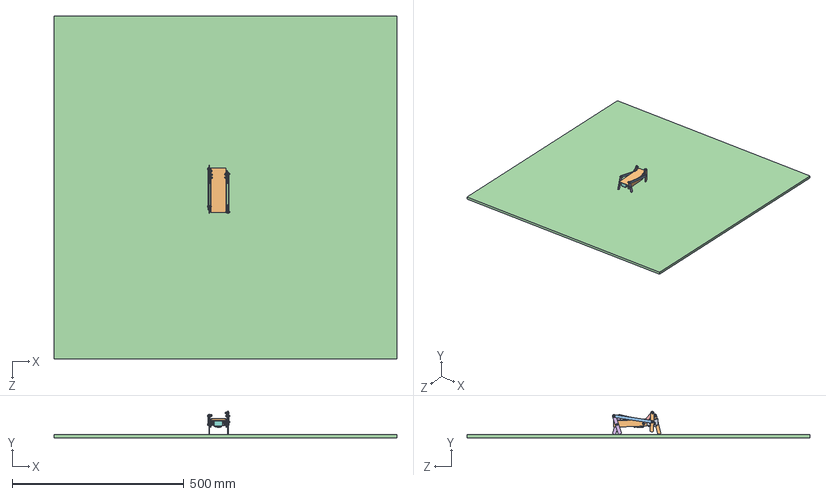
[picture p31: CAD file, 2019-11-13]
CAD/Sprint2/walking-robot-mechanism-1.snapshot.3/Walking_Robot_(assembly).SLDASM
1000.0 x 77.4 x 1000.0 mm
ELENCO GEAR BOX 01
ELENCO MOTOR HOUSING 01
ELENCO FRONT BUSHING
ELENCO MOTOR BACK 01
Terminal3V x 2
ELENCO ARMATURE 01
Enrolamento3V x 3
Walking_robot_(bolt_2_5x5) x 4
Walking_robot_(nut_2_5) x 4
Walking_robot_(main_body)
Walking_robot_(bolt_3x10) x 8
Walking_robot_(nut_3) x 18
Walking_robot_(spacer1) x 2
Walking_robot_(spacer2) x 2
Walking_robot_(bolt_3x12) x 2
PR2007 9 Volt Battery
ELENCO PINION 8T 01
SHAFT 2 X 40
pCROWN GEAR 36T X 10T R01
ELENCO COLLAR 01 x 2
pCOMPOUND GEAR 40T X 10T GREEN R01
SHAFT 3 X 52
ELENCO CRANK ARM 01 x 2
pCOMPOUND GEAR 40T X 10T GREEN R01a
pCOMPOUND GEAR 40T X 10T RED R01
Walking_robot_(legs) x 2
Walking_robot_(legs_lever1) x 2
Walking_robot_(floor)
Walking_robot_(legs_lever2) x 2
analysisWalking_robot_(legs) x 2

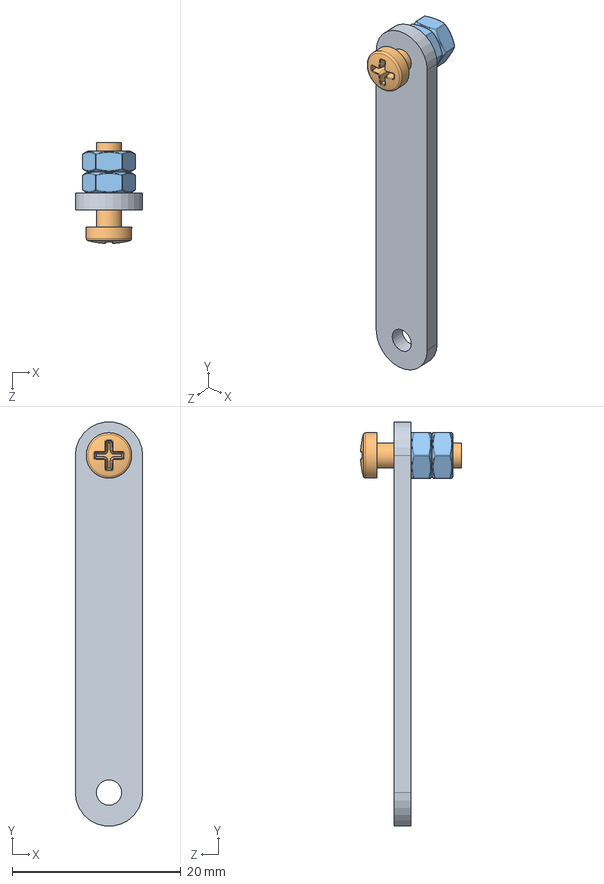
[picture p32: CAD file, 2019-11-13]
CAD/Sprint2/walking-robot-mechanism-1.snapshot.3/Walking_robot_(assembled_legs_lever2).SLDASM
8.00 x 47.9 x 12.0 mm
Walking_robot_(legs_lever2)
Walking_robot_(bolt_3x10)
Walking_robot_(nut_3) x 2

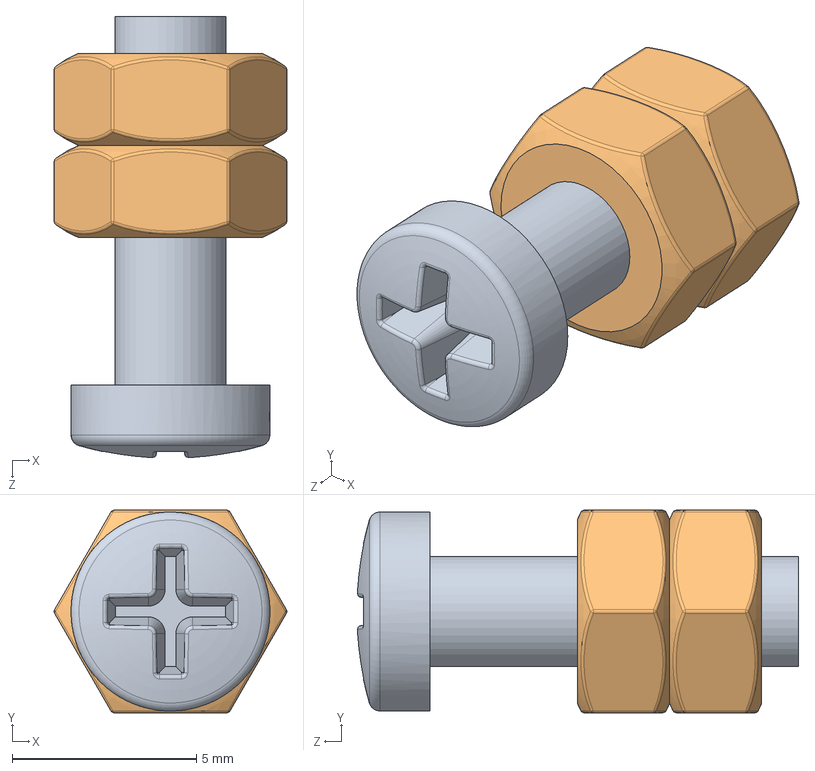
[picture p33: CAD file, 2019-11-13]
CAD/Sprint2/walking-robot-mechanism-1.snapshot.3/Walking_robot_(assembled_front_legs).SLDASM
6.32 x 5.50 x 12.0 mm
Walking_robot_(bolt_3x10)
Walking_robot_(nut_3) x 2

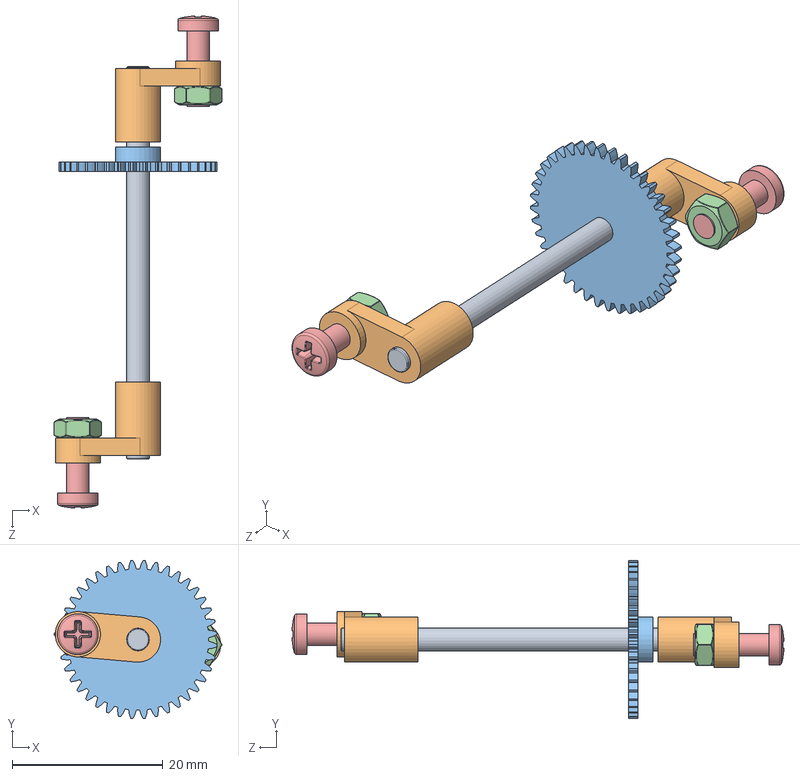
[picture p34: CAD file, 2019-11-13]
CAD/Sprint2/walking-robot-mechanism-1.snapshot.3/Walking_robot_(assembled_second_axle).SLDASM
22.3 x 21.0 x 65.2 mm
SHAFT 3 X 52
ELENCO CRANK ARM 01 x 2
pCOMPOUND GEAR 40T X 10T GREEN R01a
Walking_robot_(nut_3) x 2
Walking_robot_(bolt_3x10) x 2

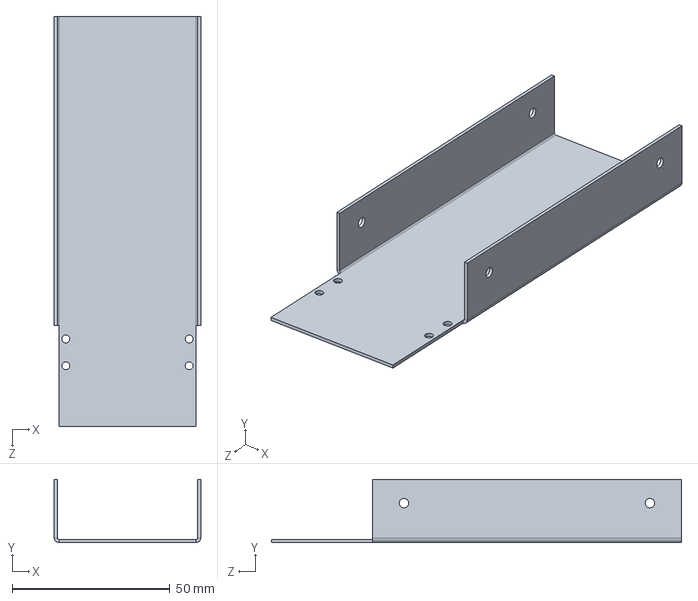
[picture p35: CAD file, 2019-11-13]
CAD/Sprint2/walking-robot-mechanism-1.snapshot.3/Walking_robot_(main_body).SLDPRT
46.5 x 20.0 x 130.0 mm

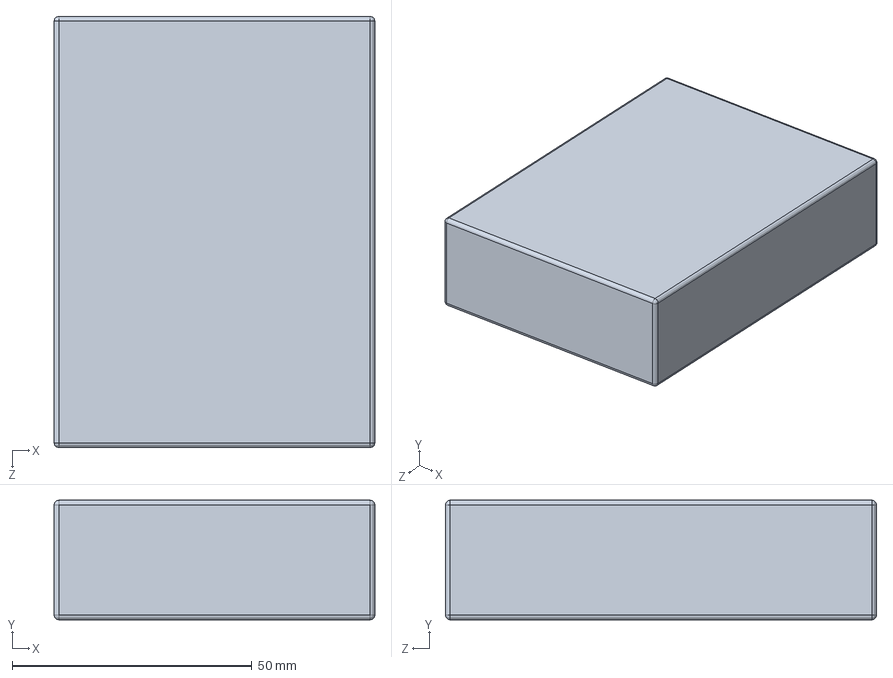
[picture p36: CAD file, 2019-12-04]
CAD/Common/Battery.SLDPRT
67.0 x 25.0 x 90.0 mm

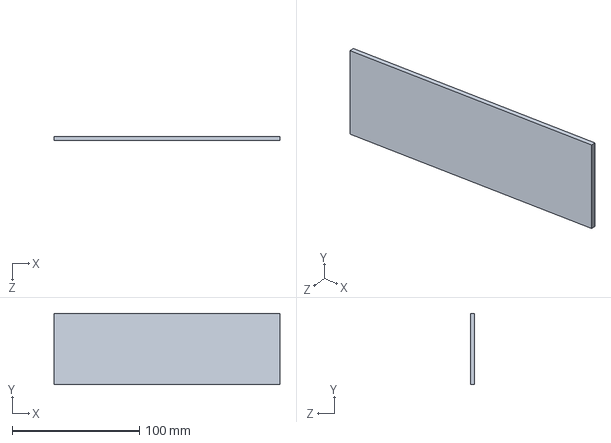
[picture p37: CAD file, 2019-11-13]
CAD/Sprint2/PoeSprint2AcrilikSkinSide.SLDPRT
177.8 x 55.9 x 3.17 mm

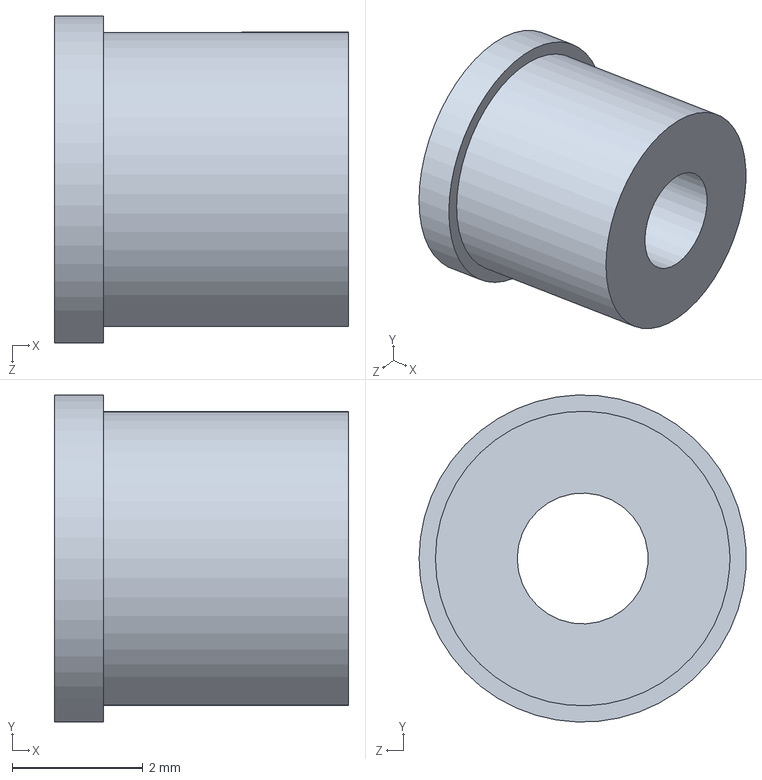
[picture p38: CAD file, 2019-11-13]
CAD/Sprint2/walking-robot-mechanism-1.snapshot.3/ELENCO COLLAR 01.SLDPRT
4.50 x 5.00 x 4.99 mm

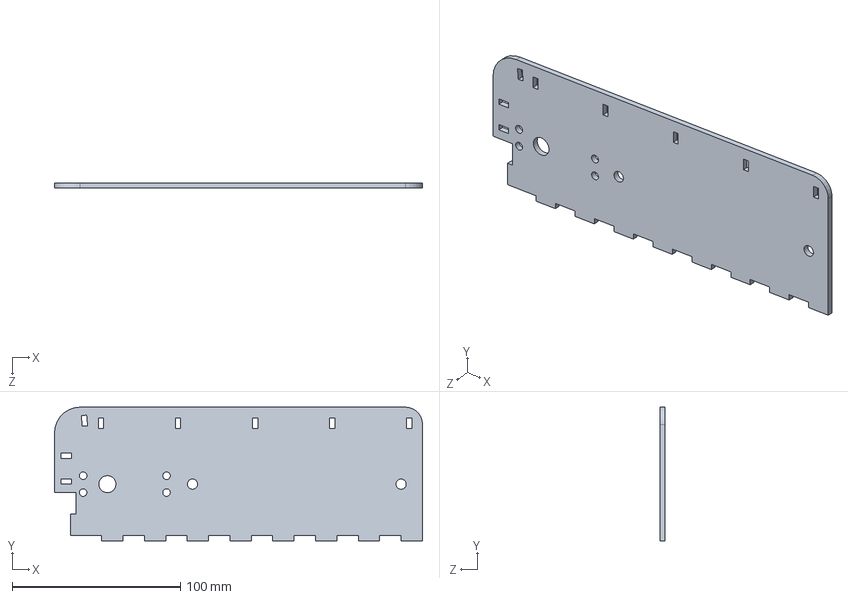
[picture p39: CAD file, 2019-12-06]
CAD/Sprint3/PoeSprint4ChasisSide.SLDPRT
218.4 x 79.4 x 3.17 mm

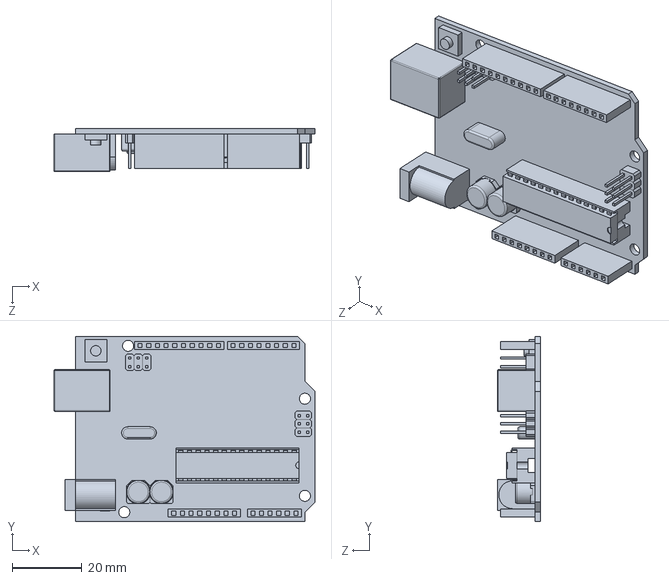
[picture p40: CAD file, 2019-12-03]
CAD/Sprint4/arduino4.SLDPRT
75.0 x 53.3 x 12.5 mm

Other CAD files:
CAD/Common/RPi cam Rev 1.3.SLDPRT
CAD/Sprint1/PoeSprint3IrSensorMount.SLDPRT
CAD/Sprint2/PoeSprint2ML.SLDPRT
CAD/Sprint3/POESprint4CameraMountHead.SLDPRT
CAD/Common/FeeTech FS5109M Metal Gear Servo Outer volume.SLDPRT
CAD/Common/PowerCircuit.SLDPRT
CAD/Common/Rpi3Bplus.SLDPRT
CAD/Common/arduino.SLDPRT
CAD/Sprint1/POEFinalSprint1Chasis - Copy.SLDPRT
CAD/Sprint1/POEFinalSprint1Chasis.SLDDRW
CAD/Sprint1/POEFinalSprint1Chasis.SLDPRT
CAD/Sprint1/PoeSpring1Foot - Copy.SLDPRT
CAD/Sprint1/PoeSpring1Foot.SLDPRT
CAD/Sprint1/PoeSrint1Leg - Copy.SLDPRT
CAD/Sprint1/PoeSrint1Leg.SLDPRT
CAD/Sprint1/PoeSrint1SensorMount - Copy.SLDPRT
CAD/Sprint1/PoeSrint1SensorMount.SLDPRT
CAD/Sprint2/POEFinalSprint2ChasiRecutCutSheet.SLDDRW
CAD/Sprint2/POEFinalSprint2CutSheet.SLDDRW
CAD/Sprint2/POEFinalSprint2CutSheetAcrilick.SLDDRW
CAD/Sprint2/PoeSprint2AcrilicSkinTop.SLDPRT
CAD/Sprint2/PoeSprint2ChasisBodie.SLDPRT
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

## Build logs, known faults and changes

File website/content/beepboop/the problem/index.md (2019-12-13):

---
title: 'The Problem'
---
Every semester, students pass through the halls of the Olin College of Engineering Academic Center sad, alone, and reminding themselves that the weekend is only a few days away. We wondered why people looked so stressed, and sometimes even sad while in this stately building and came to the conclusion that it was because there was a genuine lack of small furry robots that say hi to people.

<!--more-->

There are 75 days in a semester, and almost everyone can say that there have been 0 times when a cute robot has said hi to you. Unbelievable!

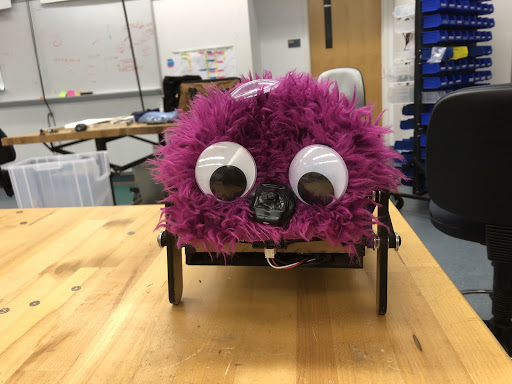
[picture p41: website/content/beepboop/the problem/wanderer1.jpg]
asdf


This is why we created The Wanderer: a cute, personable robot that will wander around the Academic Center and greet anyone it sees to brighten their day!

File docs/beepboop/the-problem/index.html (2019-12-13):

- Home
- BeepBoop
- Breakdown
- Sprints
- BOM
- Logs
- Team

 (https://naviatolin.github.io/The-Wanderer/)

 (https://naviatolin.github.io/The-Wanderer/)

- Home
- BeepBoop
- Breakdown
- Sprints
- BOM
- Logs
- Team

#### Beepboop

- The Problem (https://naviatolin.github.io/The-Wanderer/beepboop/the-problem/)
- Who Am I (https://naviatolin.github.io/The-Wanderer/beepboop/who-am-i/)

# The Problem

Every semester, students pass through the halls of the Olin College of Engineering Academic Center sad, alone, and reminding themselves that the weekend is only a few days away. We wondered why people looked so stressed, and sometimes even sad while in this stately building and came to the conclusion that it was because there was a genuine lack of small furry robots that say hi to people.

There are 75 days in a semester, and almost everyone can say that there have been 0 times when a cute robot has said hi to you. Unbelievable!

asdf

This is why we created The Wanderer: a cute, personable robot that will wander around the Academic Center and greet anyone it sees to brighten their day!

- www.zerostatic.io

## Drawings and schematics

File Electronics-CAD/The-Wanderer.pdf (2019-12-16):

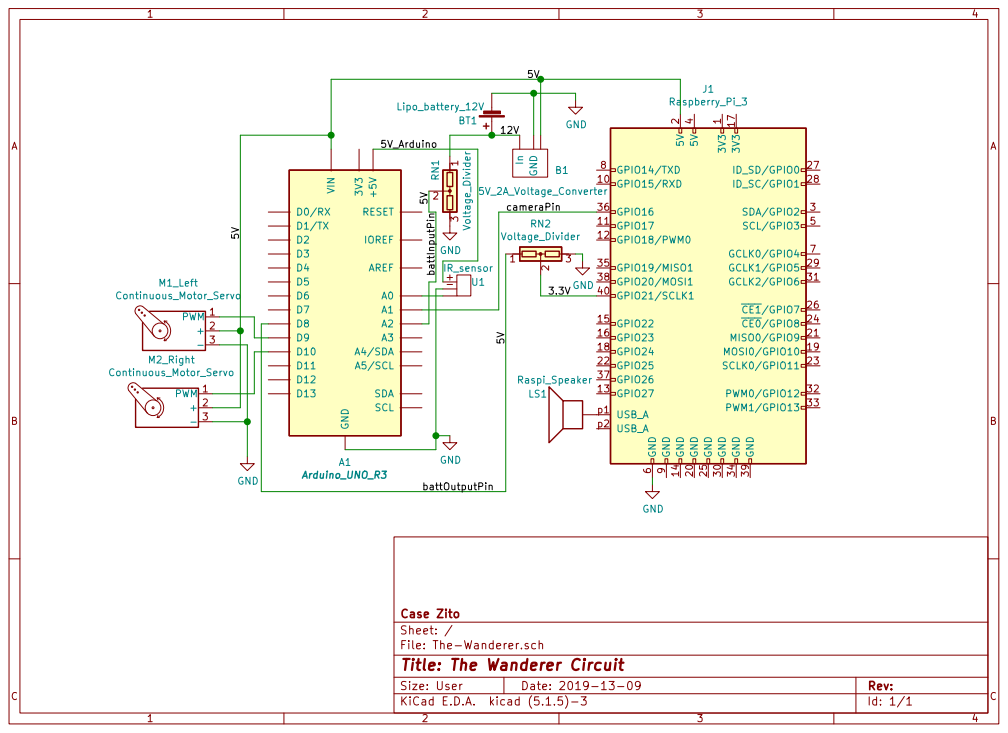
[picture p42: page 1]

Id: 1/1 Title: The Wanderer Circuit File: The-Wanderer.sch Sheet: / Case Zito

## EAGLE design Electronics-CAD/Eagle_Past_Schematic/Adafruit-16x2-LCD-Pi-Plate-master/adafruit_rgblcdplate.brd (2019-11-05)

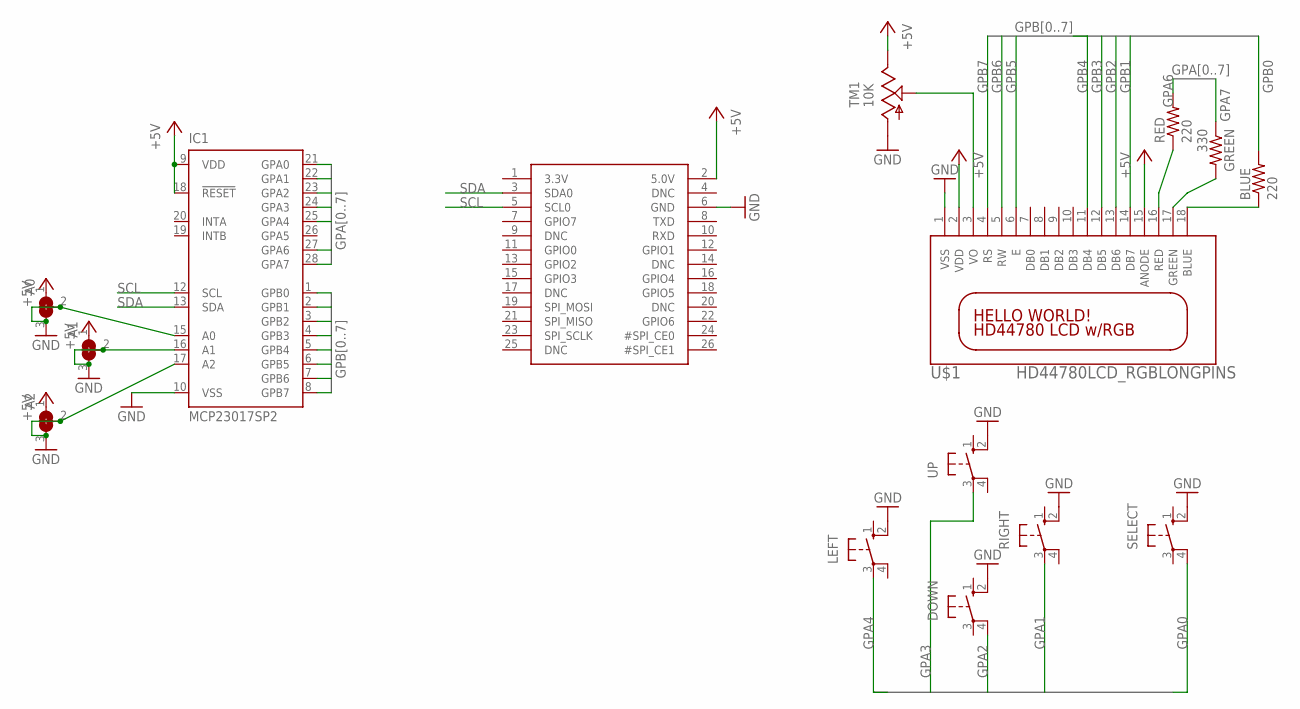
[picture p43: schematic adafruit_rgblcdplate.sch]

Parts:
A0, A1, A2: SOLDERJUMPER_2WAY; SOLDERJUMPER_2WAY_OPEN_NOPASTE
BLUE: 220; 0207/10
DOWN: 10-XX; B3F-10XX
GREEN: 330; 0207/10
IC1: MCP23017SP2; DIL28-3-ROUND
LEFT: 10-XX; B3F-10XX
RED: 220; 0207/10
RIGHT: 10-XX; B3F-10XX
SELECT: 10-XX; B3F-10XX
TM1: 10K; 6MM
U$1: HD44780LCD_RGBLONGPINS; LCD1602-RGB
U$4: RASPBERRYPI_BB; RASBERRYPI_SHIELD
UP: 10-XX; B3F-10XX

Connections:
+5V: A0.1, A1.1, A2.1, IC1.9 (VDD), IC1.18 (!RESET), TM1.E, U$1.2 (VDD), U$1.15 (ANODE), U$4.2 (5.0V)
GND: A0.2, A0.3, A1.2, A1.3, A2.2, A2.3, DOWN.2 (S1), IC1.10 (VSS), IC1.15 (A0), IC1.16 (A1), IC1.17 (A2), LEFT.2 (S1), RIGHT.2 (S1), SELECT.2 (S1), TM1.A, U$1.1 (VSS), U$4.6 (GND), UP.2 (S1)
GPA0: IC1.21 (GPA0), SELECT.4 (P1)
GPA1: IC1.22 (GPA1), RIGHT.3
GPA2: DOWN.4 (P1), IC1.23 (GPA2)
GPA3: IC1.24 (GPA3), UP.3
GPA4: IC1.25 (GPA4), LEFT.3
GPA6: IC1.27 (GPA6), RED.2
GPA7: GREEN.1, IC1.28 (GPA7)
GPB0: BLUE.2, IC1.1 (GPB0)
GPB1: IC1.2 (GPB1), U$1.14 (DB7)
GPB2: IC1.3 (GPB2), U$1.13 (DB6)
GPB3: IC1.4 (GPB3), U$1.12 (DB5)
GPB4: IC1.5 (GPB4), U$1.11 (DB4)
GPB5: IC1.6 (GPB5), U$1.6 (E)
GPB6: IC1.7 (GPB6), U$1.5 (RW)
GPB7: IC1.8 (GPB7), U$1.4 (RS)
unnamed: BLUE.1, U$1.18 (BLUE)
unnamed: GREEN.2, U$1.17 (GREEN)
unnamed: RED.1, U$1.16 (RED)
unnamed: TM1.S, U$1.3 (VO)
SCL: IC1.12 (SCL), U$4.5 (SCL0)
SDA: IC1.13 (SDA), U$4.3 (SDA0)

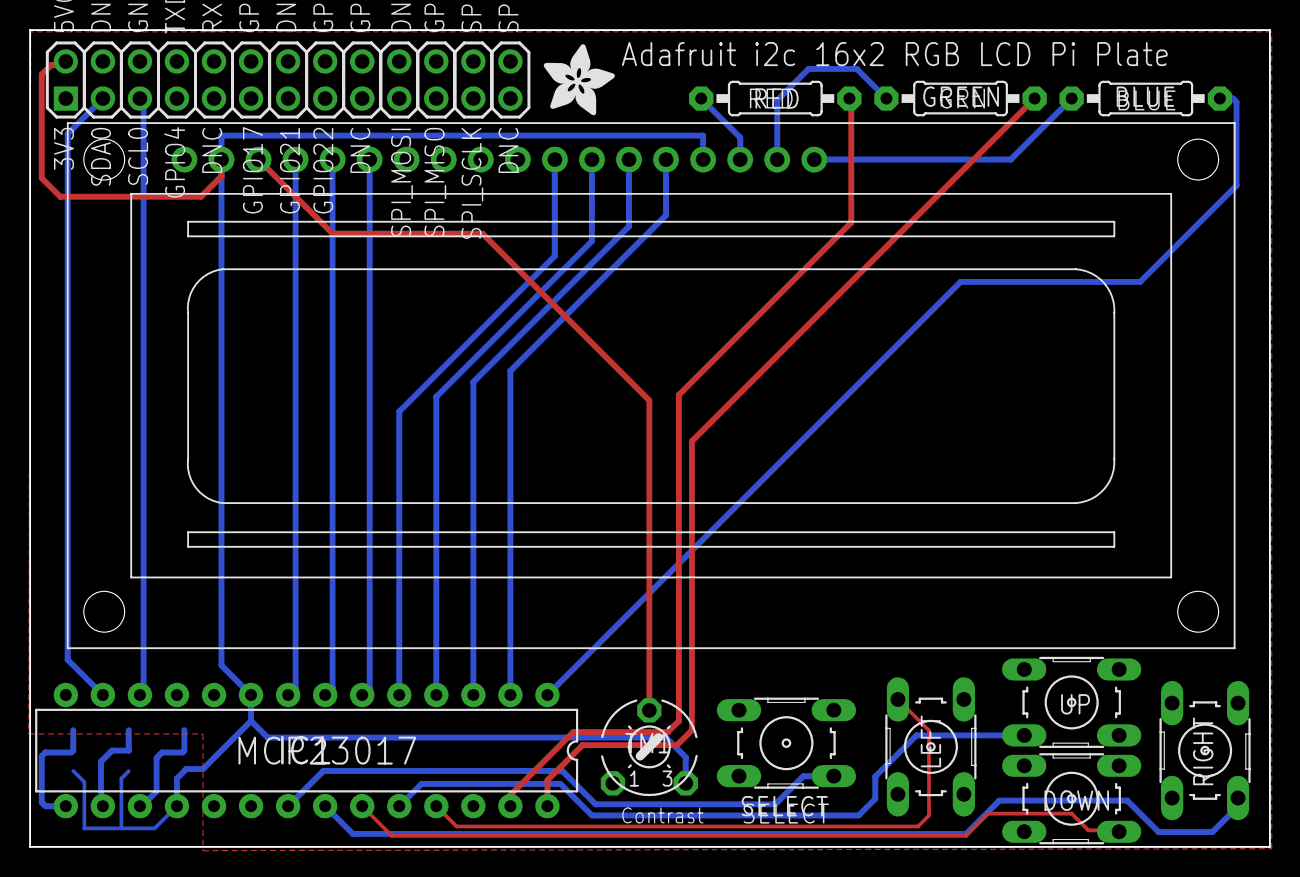
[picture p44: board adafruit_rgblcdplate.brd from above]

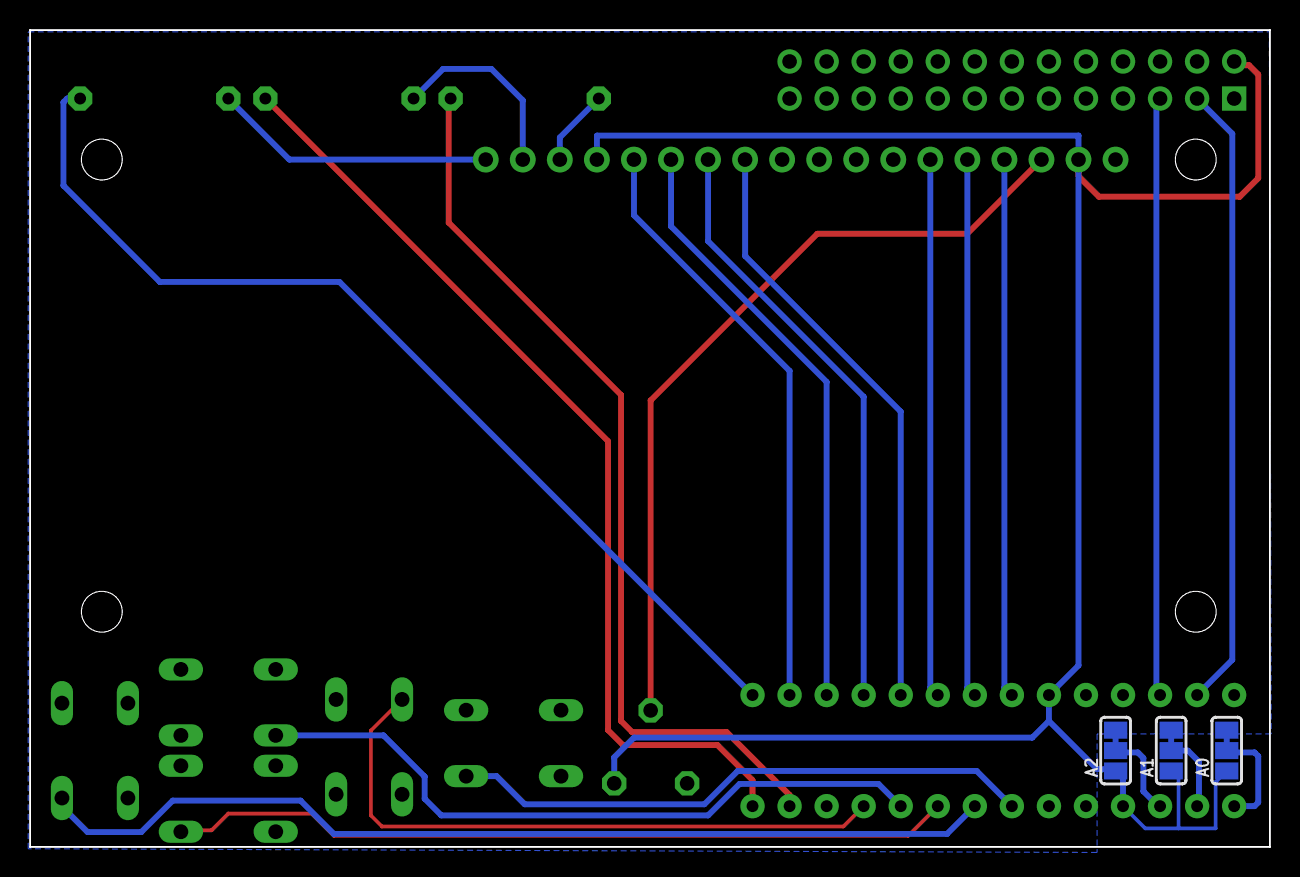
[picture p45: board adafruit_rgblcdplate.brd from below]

Board: 2 copper layers, 85.0 x 56.0 mm, 16 parts (3 on the bottom side), 23 nets.

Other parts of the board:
U$2: ADAFRUIT_5MM

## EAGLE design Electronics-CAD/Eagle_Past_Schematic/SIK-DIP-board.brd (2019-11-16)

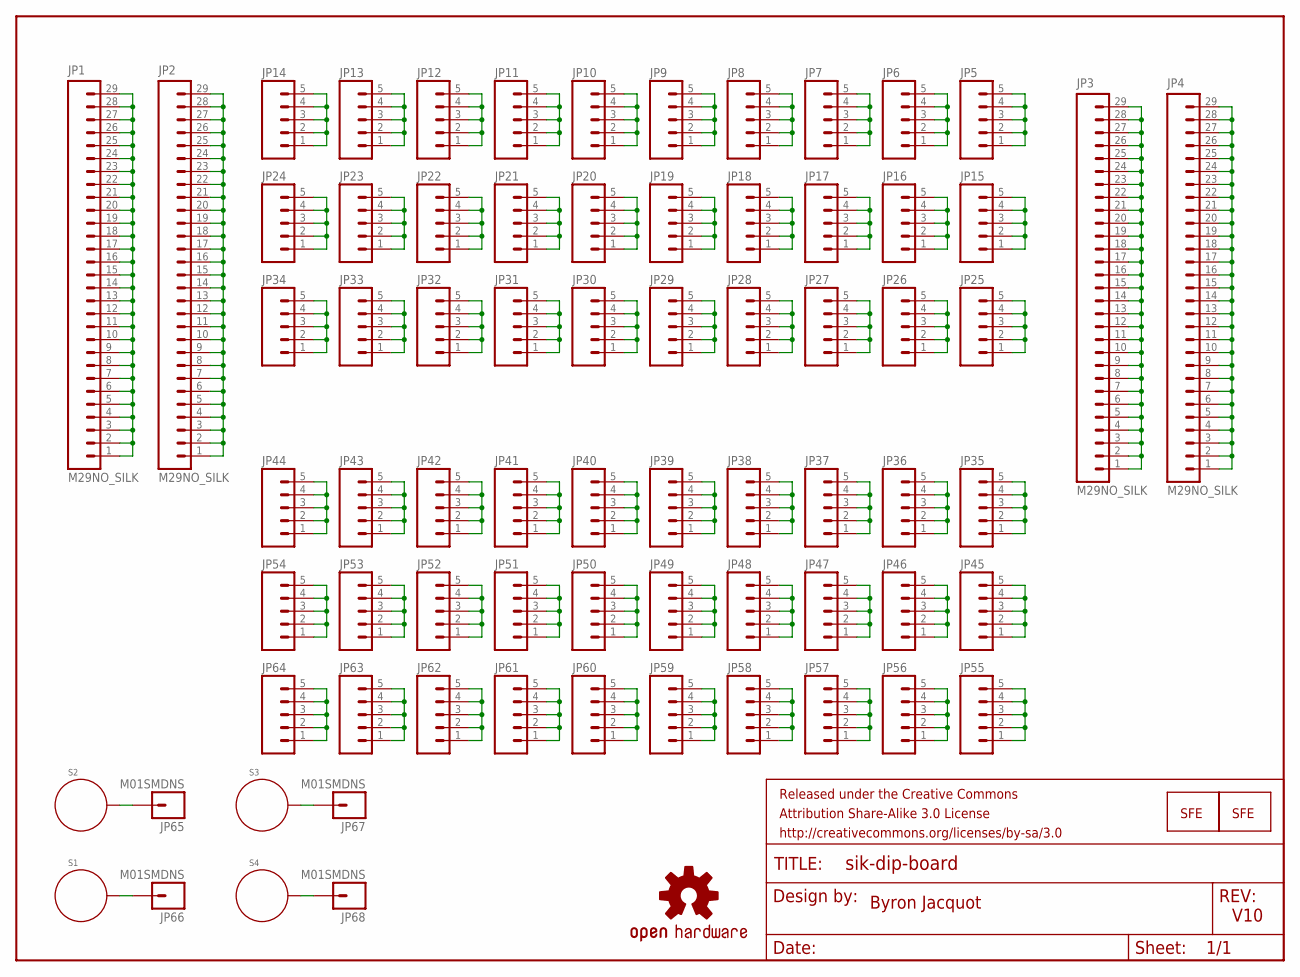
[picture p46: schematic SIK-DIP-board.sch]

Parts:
FRAME1: FRAME-LETTER; CREATIVE_COMMONS
JP1, JP2, JP3, JP4: M29NO_SILK; 1X29_NO_SILK
JP5, JP6, JP7, JP8, JP9, JP10, JP11, JP12, JP13, JP14, JP15, JP16, JP17, JP18, JP19, JP20, JP21, JP22, JP23, JP24, JP25, JP26, JP27, JP28, JP29, JP30, JP31, JP32, JP33, JP34, JP35, JP36, JP37, JP38, JP39, JP40, JP41, JP42, JP43, JP44, JP45, JP46, JP47, JP48, JP49, JP50, JP51, JP52, JP53, JP54, JP55, JP56, JP57, JP58, JP59, JP60, JP61, JP62, JP63, JP64: M05NO_SILK; 1X05_NO_SILK
JP65, JP66, JP67, JP68: M01SMDNS; 1X01NS
LOGO1: LOGO-SFECP; SFE-LOGO-FLAME-COPPER
LOGO2: LOGO-SFENEW; SFE-NEW-WEBLOGO
LOGO3: OSHW-LOGOS; OSHW-LOGO-S
S1, S2, S3, S4: STANDOFF_ELECTRICAL; STANDOFF-ELECTRICAL

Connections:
unnamed: JP1.1, JP1.2, JP1.3, JP1.4, JP1.5, JP1.6, JP1.7, JP1.8, JP1.9, JP1.10, JP1.11, JP1.12, JP1.13, JP1.14, JP1.15, JP1.16, JP1.17, JP1.18, JP1.19, JP1.20, JP1.21, JP1.22, JP1.23, JP1.24, JP1.25, JP1.26, JP1.27, JP1.28, JP1.29
unnamed: JP2.1, JP2.2, JP2.3, JP2.4, JP2.5, JP2.6, JP2.7, JP2.8, JP2.9, JP2.10, JP2.11, JP2.12, JP2.13, JP2.14, JP2.15, JP2.16, JP2.17, JP2.18, JP2.19, JP2.20, JP2.21, JP2.22, JP2.23, JP2.24, JP2.25, JP2.26, JP2.27, JP2.28, JP2.29
unnamed: JP3.1, JP3.2, JP3.3, JP3.4, JP3.5, JP3.6, JP3.7, JP3.8, JP3.9, JP3.10, JP3.11, JP3.12, JP3.13, JP3.14, JP3.15, JP3.16, JP3.17, JP3.18, JP3.19, JP3.20, JP3.21, JP3.22, JP3.23, JP3.24, JP3.25, JP3.26, JP3.27, JP3.28, JP3.29
unnamed: JP4.1, JP4.2, JP4.3, JP4.4, JP4.5, JP4.6, JP4.7, JP4.8, JP4.9, JP4.10, JP4.11, JP4.12, JP4.13, JP4.14, JP4.15, JP4.16, JP4.17, JP4.18, JP4.19, JP4.20, JP4.21, JP4.22, JP4.23, JP4.24, JP4.25, JP4.26, JP4.27, JP4.28, JP4.29
unnamed: JP10.1, JP10.2, JP10.3, JP10.4, JP10.5
unnamed: JP5.1, JP5.2, JP5.3, JP5.4, JP5.5
unnamed: JP6.1, JP6.2, JP6.3, JP6.4, JP6.5
unnamed: JP7.1, JP7.2, JP7.3, JP7.4, JP7.5
unnamed: JP8.1, JP8.2, JP8.3, JP8.4, JP8.5
unnamed: JP9.1, JP9.2, JP9.3, JP9.4, JP9.5
unnamed: JP11.1, JP11.2, JP11.3, JP11.4, JP11.5
unnamed: JP12.1, JP12.2, JP12.3, JP12.4, JP12.5
unnamed: JP13.1, JP13.2, JP13.3, JP13.4, JP13.5
unnamed: JP14.1, JP14.2, JP14.3, JP14.4, JP14.5
unnamed: JP15.1, JP15.2, JP15.3, JP15.4, JP15.5
unnamed: JP16.1, JP16.2, JP16.3, JP16.4, JP16.5
unnamed: JP17.1, JP17.2, JP17.3, JP17.4, JP17.5
unnamed: JP18.1, JP18.2, JP18.3, JP18.4, JP18.5
unnamed: JP19.1, JP19.2, JP19.3, JP19.4, JP19.5
unnamed: JP20.1, JP20.2, JP20.3, JP20.4, JP20.5
unnamed: JP21.1, JP21.2, JP21.3, JP21.4, JP21.5
unnamed: JP22.1, JP22.2, JP22.3, JP22.4, JP22.5
unnamed: JP23.1, JP23.2, JP23.3, JP23.4, JP23.5
unnamed: JP24.1, JP24.2, JP24.3, JP24.4, JP24.5
unnamed: JP25.1, JP25.2, JP25.3, JP25.4, JP25.5
unnamed: JP26.1, JP26.2, JP26.3, JP26.4, JP26.5
unnamed: JP27.1, JP27.2, JP27.3, JP27.4, JP27.5
unnamed: JP28.1, JP28.2, JP28.3, JP28.4, JP28.5
unnamed: JP29.1, JP29.2, JP29.3, JP29.4, JP29.5
unnamed: JP30.1, JP30.2, JP30.3, JP30.4, JP30.5
unnamed: JP31.1, JP31.2, JP31.3, JP31.4, JP31.5
unnamed: JP32.1, JP32.2, JP32.3, JP32.4, JP32.5
unnamed: JP33.1, JP33.2, JP33.3, JP33.4, JP33.5
unnamed: JP34.1, JP34.2, JP34.3, JP34.4, JP34.5
unnamed: JP35.1, JP35.2, JP35.3, JP35.4, JP35.5
unnamed: JP36.1, JP36.2, JP36.3, JP36.4, JP36.5
unnamed: JP37.1, JP37.2, JP37.3, JP37.4, JP37.5
unnamed: JP38.1, JP38.2, JP38.3, JP38.4, JP38.5
unnamed: JP39.1, JP39.2, JP39.3, JP39.4, JP39.5
unnamed: JP40.1, JP40.2, JP40.3, JP40.4, JP40.5
unnamed: JP41.1, JP41.2, JP41.3, JP41.4, JP41.5
unnamed: JP42.1, JP42.2, JP42.3, JP42.4, JP42.5
unnamed: JP43.1, JP43.2, JP43.3, JP43.4, JP43.5
unnamed: JP44.1, JP44.2, JP44.3, JP44.4, JP44.5
unnamed: JP45.1, JP45.2, JP45.3, JP45.4, JP45.5
unnamed: JP46.1, JP46.2, JP46.3, JP46.4, JP46.5
unnamed: JP47.1, JP47.2, JP47.3, JP47.4, JP47.5
unnamed: JP48.1, JP48.2, JP48.3, JP48.4, JP48.5
unnamed: JP49.1, JP49.2, JP49.3, JP49.4, JP49.5
unnamed: JP50.1, JP50.2, JP50.3, JP50.4, JP50.5
unnamed: JP51.1, JP51.2, JP51.3, JP51.4, JP51.5
unnamed: JP52.1, JP52.2, JP52.3, JP52.4, JP52.5
unnamed: JP53.1, JP53.2, JP53.3, JP53.4, JP53.5
unnamed: JP54.1, JP54.2, JP54.3, JP54.4, JP54.5
unnamed: JP55.1, JP55.2, JP55.3, JP55.4, JP55.5
unnamed: JP56.1, JP56.2, JP56.3, JP56.4, JP56.5
unnamed: JP57.1, JP57.2, JP57.3, JP57.4, JP57.5
unnamed: JP58.1, JP58.2, JP58.3, JP58.4, JP58.5
unnamed: JP59.1, JP59.2, JP59.3, JP59.4, JP59.5
unnamed: JP60.1, JP60.2, JP60.3, JP60.4, JP60.5
unnamed: JP61.1, JP61.2, JP61.3, JP61.4, JP61.5
unnamed: JP62.1, JP62.2, JP62.3, JP62.4, JP62.5
unnamed: JP63.1, JP63.2, JP63.3, JP63.4, JP63.5
unnamed: JP64.1, JP64.2, JP64.3, JP64.4, JP64.5
unnamed: JP65.1, S2.P1
unnamed: JP66.1, S1.P1
unnamed: JP67.1, S3.P1
unnamed: JP68.1, S4.P1

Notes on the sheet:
Byron Jacquot
V10

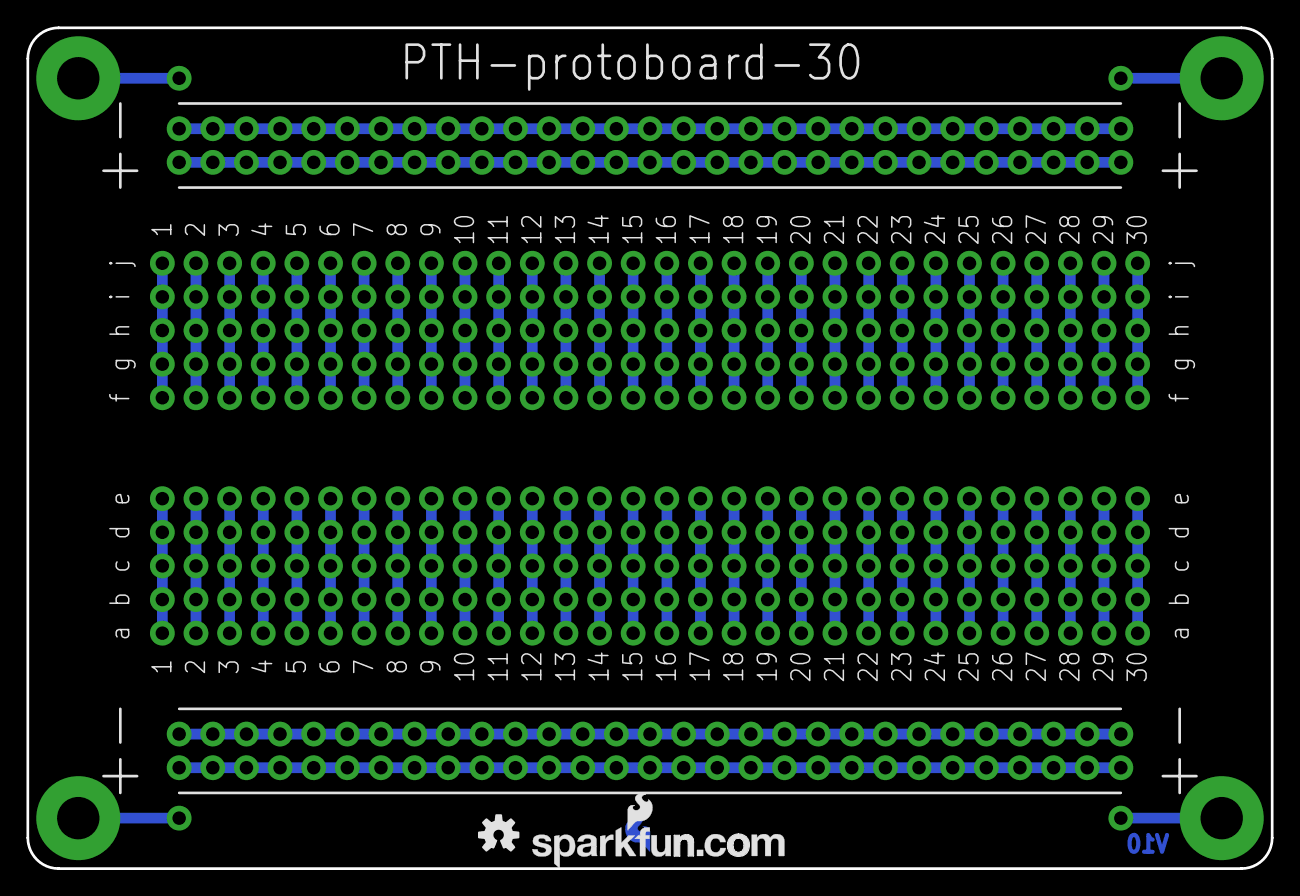
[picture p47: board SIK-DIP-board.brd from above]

Board: 2 copper layers, 94.0 x 63.5 mm, 76 parts (1 on the bottom side), 68 nets.

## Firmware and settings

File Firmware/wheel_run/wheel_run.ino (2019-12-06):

//import libraries
#include <Servo.h>
#include <Wire.h>

//create instances of Servo class for legs
Servo leftLeg;
Servo rightLeg;
//variables for motor speed and sensors
int leftSpeed = 60; //starting speed for motors, is forward <90, 0 is full speed
int rightSpeed = 180-leftSpeed;

//prox sensor
#define prox_sensor A0
int distance = 0;

//Raspi communication
int cameraPin = A1; //notification from raspi for seeing a person 
int battInputPin = A2; //reads the current battery voltage
int battOutputPin = 8; //outputs a battery low signal to raspi
float battVolt = 0;  //to track battery voltage

float getBatteryVoltage(int batteryPin){
  // Convert the analogRead to battery voltage
  // 5V / 1024 to go from Arduino ADC to Measured Voltage
  // *4.34 to go from Measured Voltage to Battery Voltage
  // (Divider divides by 4.34)
  return (float)analogRead(batteryPin) * 5 * 4.34 / 1024;
}

void setup() {
  leftLeg.attach(9);
  rightLeg.attach(10);
  pinMode(battOutputPin, OUTPUT);
  Serial.begin(9600);
}

void loop() {
  battVolt = getBatteryVoltage(battInputPin); // read battery voltage
  Serial.print("Battery reading: ");
  Serial.println(battVolt);
  digitalWrite(battOutputPin, battVolt < 11.5); //Indicate high if battery voltage is less than 11.5

  //Serial.print("Distance: ");
  //Serial.println(distance);
  distance = analogRead(prox_sensor);

  //Serial.print("Seen: ");
  Serial.println(analogRead(cameraPin)>=170);
  if (analogRead(cameraPin)>=170){ // Robot stops when speaker is being used
    Serial.println("Stopped while talking");
    leftLeg.write(90);
    rightLeg.write(90);
  }
  else if (distance > 300) {
    Serial.println("Turning, distance > 300");
    leftLeg.write(140); // one of the motors is reverse polarity, so one wheel goes backwards
    rightLeg.write(140);
  }
  else if (analogRead(cameraPin)<170){
    Serial.println("Going Forward");
    //Serial.print("Speed: ");
    //Serial.println(rightSpeed);
    leftLeg.write(leftSpeed);
    rightLeg.write(rightSpeed);
  }
}

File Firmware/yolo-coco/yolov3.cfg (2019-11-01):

[net]
# Testing
# batch=1
# subdivisions=1
# Training
batch=64
subdivisions=16
width=200
height=200
channels=3
momentum=0.9
decay=0.0005
angle=0
saturation = 1.5
exposure = 1.5
hue=.1

learning_rate=0.001
burn_in=1000
max_batches = 500200
policy=steps
steps=400000,450000
scales=.1,.1

[convolutional]
batch_normalize=1
filters=32
size=3
stride=1
pad=1
activation=leaky

# Downsample

[convolutional]
batch_normalize=1
filters=64
size=3
stride=2
pad=1
activation=leaky

[convolutional]
batch_normalize=1
filters=32
size=1
stride=1
pad=1
activation=leaky

[convolutional]
batch_normalize=1
filters=64
size=3
stride=1
pad=1
activation=leaky

[shortcut]
from=-3
activation=linear

# Downsample

[convolutional]
batch_normalize=1
filters=128
size=3
stride=2
pad=1
activation=leaky

[convolutional]
batch_normalize=1
filters=64
size=1
stride=1
pad=1
activation=leaky

[convolutional]
batch_normalize=1
filters=128
size=3
stride=1
pad=1
activation=leaky

[shortcut]
from=-3
activation=linear

[convolutional]
batch_normalize=1
filters=64
size=1
stride=1
pad=1
activation=leaky

[convolutional]
batch_normalize=1
filters=128
size=3
stride=1
pad=1
activation=leaky

[shortcut]
from=-3
activation=linear

# Downsample

[convolutional]
batch_normalize=1
filters=256
size=3
stride=2
pad=1
activation=leaky

[convolutional]
batch_normalize=1
filters=128
size=1
stride=1
pad=1
activation=leaky

[convolutional]
batch_normalize=1
filters=256
size=3
stride=1
pad=1
activation=leaky

[shortcut]
from=-3
activation=linear

[convolutional]
batch_normalize=1
filters=128
size=1
stride=1
pad=1
activation=leaky

[convolutional]
batch_normalize=1
filters=256
size=3
stride=1
pad=1
activation=leaky

[shortcut]
from=-3
activation=linear

[convolutional]
batch_normalize=1
filters=128
size=1
stride=1
pad=1
activation=leaky

[convolutional]
batch_normalize=1
filters=256
size=3
stride=1
pad=1
activation=leaky

[shortcut]
from=-3
activation=linear

[convolutional]
batch_normalize=1
filters=128
size=1
stride=1
pad=1
activation=leaky

[convolutional]
batch_normalize=1
filters=256
size=3
stride=1
pad=1
activation=leaky

[shortcut]
from=-3
activation=linear


[convolutional]
batch_normalize=1
filters=128
size=1
stride=1
pad=1
activation=leaky

[convolutional]
batch_normalize=1
filters=256
size=3
stride=1
pad=1
activation=leaky

[shortcut]
from=-3
activation=linear

[convolutional]
batch_normalize=1
filters=128
size=1
stride=1
pad=1
activation=leaky

[convolutional]
batch_normalize=1
filters=256
size=3
stride=1
pad=1
activation=leaky

[shortcut]
from=-3
activation=linear

[convolutional]
batch_normalize=1
filters=128
size=1
stride=1
pad=1
activation=leaky

[convolutional]
batch_normalize=1
filters=256
size=3
stride=1
pad=1
activation=leaky

[shortcut]
from=-3
activation=linear

[convolutional]
batch_normalize=1
filters=128
size=1
stride=1
pad=1
activation=leaky

[convolutional]
batch_normalize=1
filters=256
size=3
stride=1
pad=1
activation=leaky

[shortcut]
from=-3
activation=linear

# Downsample

[convolutional]
batch_normalize=1
filters=512
size=3
stride=2
pad=1
activation=leaky

[convolutional]
batch_normalize=1
filters=256
size=1
stride=1
pad=1
activation=leaky

[convolutional]
batch_normalize=1
filters=512
size=3
stride=1
pad=1
activation=leaky

[shortcut]
from=-3
activation=linear


[convolutional]
batch_normalize=1
filters=256
size=1
stride=1
pad=1
activation=leaky

[convolutional]
batch_normalize=1
filters=512
size=3
stride=1
pad=1
activation=leaky

[shortcut]
from=-3
activation=linear


[convolutional]
batch_normalize=1
filters=256
size=1
stride=1
pad=1
activation=leaky

[convolutional]
batch_normalize=1
filters=512
size=3
stride=1
pad=1
activation=leaky

[shortcut]
from=-3
activation=linear


[convolutional]
batch_normalize=1
filters=256
size=1
stride=1
pad=1
activation=leaky

[convolutional]
batch_normalize=1
filters=512
size=3
stride=1
pad=1
activation=leaky

[shortcut]
from=-3
activation=linear

[convolutional]
batch_normalize=1
filters=256
size=1
stride=1
pad=1
activation=leaky

[convolutional]
batch_normalize=1
filters=512
size=3
stride=1
pad=1
activation=leaky

[shortcut]
from=-3
activation=linear


[convolutional]
batch_normalize=1
filters=256
size=1
stride=1
pad=1
activation=leaky

[convolutional]
batch_normalize=1
filters=512
size=3
stride=1
pad=1
activation=leaky

[shortcut]
from=-3
activation=linear


[convolutional]
batch_normalize=1
filters=256
size=1
stride=1
pad=1
activation=leaky

[convolutional]
batch_normalize=1
filters=512
size=3
stride=1
pad=1
activation=leaky

[shortcut]
from=-3
activation=linear

[convolutional]
batch_normalize=1
filters=256
size=1
stride=1
pad=1
activation=leaky

[convolutional]
batch_normalize=1
filters=512
size=3
stride=1
pad=1
activation=leaky

[shortcut]
from=-3
activation=linear

# Downsample

[convolutional]
batch_normalize=1
filters=1024
size=3
stride=2
pad=1
activation=leaky

[convolutional]
batch_normalize=1
filters=512
size=1
stride=1
pad=1
activation=leaky
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

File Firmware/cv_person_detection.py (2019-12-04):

"""
Contains all the classes used for computer vision and backend processing.

@author: Duncan Mazza
Stripped down for Raspi by Michael Remley
@revision: v1.4
"""
# pip install opencv-python
# pip install opencv-contrib-python
import cv2
from math import acos, cos, sin
import numpy as np
import os


class ProcessingEngine:
    """
    The backend class for image per-processing.
    """

    def __init__(self, threshold=30, debug=False):
        # load the COCO class labels our YOLO model was trained on
        cwd = os.getcwd()
        self.DETECTION_THRESHOLD = 0.4  # minimum confidence level for person to be recognized
        print(cwd)

        labelsPath = "/home/pi/The-Wanderer/Firmware/yolo-coco/coco.names"

        self.weightsPath = "/home/pi/The-Wanderer/Firmware/yolo-coco/yolov3.weights"
        self.configPath = "/home/pi/The-Wanderer/Firmware/yolo-coco/yolov3.cfg"
        self.LABELS = open(labelsPath).read().strip().split("\n")

        self.ln = 0  # a placeholder (for determining only the *output* layer names that we need from YOLO)
        # that is overridden when self.turn_on() is called

        self.n = 0  # counter for the calibration process
        self.threshold = threshold  # minimum number of frames used to perform calibration

        self.debug = debug

        self.cap_dict = {}  # store the OpenCV captures in a dictionary
        self.detect_dict = {}  # store detected outputs in a dictionary

        self.sees_person = False

        # How closely to look at the image, 1:(320,320) looks closer than 2:(128,128)
        self.reading_frames = {1: (320, 320), 2: (128, 128), 3: (96, 96), 4:(32,32)}

    def turn_on(self):
        """
        This method loads all of the OpenCV camera captures into self.cap_dict and, and also loads all of the
        objects used for detection and stores them in self.detect_dict. One of the main purposes of this function is
        so that the camera(s) is/are not turned on until the select_feeds.html file is opened.
        :param filename: path to the video file being uploaded if not using the live camera footage
        :return:
        """
        cap = cv2.VideoCapture(0)
        if cap.isOpened():
            # Representation of dictionary entries: [OpenCV capture, calibration boolean, 0 which is a placeholder
            # for the calibration matrix, 1, which is boolean for whether the camera is to be used, and (height,
            # width) of the camera frame]
            self.cap_dict = [cap, 0, 0, 1, (int(cap.get(cv2.CAP_PROP_FRAME_HEIGHT)),
                                               int(cap.get(cv2.CAP_PROP_FRAME_WIDTH)))]
            print("[INFO] loading YOLO from disk for camera {}...".format(0))
            self.detect_dict = cv2.dnn.readNetFromDarknet(self.configPath,
                                                             self.weightsPath)  # load our YOLO object detector trained on COCO dataset (80 classes)
            print("[INFO] finished loading YOLO for camera {}...".format(0))
            # the following part only needs to be initialized once, but it is in this for loop because
            #  the at least one cv2.dnn.readNetFromDarknet(...) has to have been initialized for this part to
            # be initialized.

            # determine only the *output* layer names that we need from YOLO
            self.ln = self.detect_dict.getLayerNames()
            self.ln = [self.ln[i[0] - 1] for i in self.detect_dict.getUnconnectedOutLayers()]

    def turn_off(self):
        """
        Releases the OpenCV device and clears the appropriate attributes from the class.
        :return: void
        """

        self.cap_dict.release()
        self.cap_dict = {}

    def _parse_detected(self, frame, layerOutputs):
        """
        This function takes the output of the object detection and parses the information down to bounding box
        coordinates of any people that the algorithm detects.

        This method was derived from the example at this link:
        https://www.pyimagesearch.com/2018/11/12/yolo-object-detection-with-opencv/
        credit to: Adrian Rosebrock

        :param frame: input frame to the object detection
        :param w: width of the frame
        :param h: height of the frame
        :param layerOutputs: output from the object detection
        :param LABELS: labels for the YOLO model
        :return: boxes, frame_copy: bounding boxes for the detected people, a copy of the frame with bounding boxes
        drawn
        """
        boxes = []
        confidences = []
        classIDs = []

        # frame width and height
        W = self.cap_dict[4][1]
        H = self.cap_dict[4][0]

        # loop over each of the layer outputs
        for output in layerOutputs:
            # loop over each of the detections
            for detection in output:
                # extract the class ID and confidence (i.e., probability) of the current object detection
                scores = detection[5:]
                classID = np.argmax(scores)

                confidence = scores[classID]

                # filter out weak predictions by ensuring the detected probability is greater than the minimum
                # probability
                if confidence > self.DETECTION_THRESHOLD:
                    # scale the bounding box coordinates back relative to the size of the image, keeping in mind that
                    # YOLO actually returns the center (x, y)-coordinates of the bounding box followed by the boxes'
                    # width and height
                    box = detection[0:4] * np.array([W, H, W, H])
                    (centerX, centerY, width, height) = box.astype("int")

                    # use the center (x, y)-coordinates to derive the top and left corner of the bounding box
                    x = int(centerX - (width / 2))
                    y = int(centerY - (height / 2))

                    # update our list of bounding box coordinates, confidences, and class IDs
                    boxes.append([x, y, int(width), int(height)])
                    confidences.append(float(confidence))
                    classIDs.append(classID)

        # apply non-maxima suppression to suppress weak, overlapping bounding boxes
        idxs = cv2.dnn.NMSBoxes(boxes, confidences, self.DETECTION_THRESHOLD, 0.3)

        # ensure at least one detection exists
        if len(idxs) > 0:
            # loop over the indexes we are keeping
            for i in idxs.flatten():
                if self.LABELS[classIDs[i]] != 'person':
                    frame_copy = frame
                    return [], frame_copy
                else:
                    self.sees_person = True
                    # extract the bounding box coordinates
                    (x, y) = (boxes[i][0], boxes[i][1])
                    (w, h) = (boxes[i][2], boxes[i][3])
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

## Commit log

2019-10-17 Add CAD folder
2019-10-18 Add Arduino code to run motors on robot
2019-10-22 Remove unnecessary code from wheel_run
2019-10-22 Update code to print out when wheels are turning
    Fixed compile issues as well
    [wheel_run.ino]
2019-10-24 Add cv_person_detction
    cv_person_detection uses opencv to load a webcam feed and detect people in it. You'll need to yolov3.weights file, which is too big to store on github
    [yolov3.cfg]
2019-10-24 Create electrical schematic draft
    [The-Wanderer.sch]
2019-11-03 Update schematic CAD
    Add a mockup the raspi pins
    [adafruit_rgblcdplate.brd, adafruit_rgblcdplate.sch]
2019-11-05 arduino code
2019-11-05 Attempt i2c with computer vision
    [yolov3.cfg]
2019-11-05 Fixing import issue in i2c_demo_rpi
    [cv_person_detection.py, i2c_demo_rpi.py]
2019-11-05 Updating i2c_deom_rpi to Python3
2019-11-05 Updating .gitignore
    [yolov3.cfg]
2019-11-08 Fix cv_person_detection.py
    DETECTION_THRESHOLD must be defined at the global scope
    [cv_person_detection.py]
2019-11-08 Add person_detected attribute to ProcessingEngine
    When called as a module, call person_detected to see if there is a person currently in view
2019-11-08 Make i2c_demo_rpi show person detected status on Arduino
    Also doesn't call imshow, so does not need a screen to function
    [i2c_demo_rpi.py]
2019-11-12 Modify detection thershold and reading frame
2019-11-13 Add all CAD files
    [Arm01.step.SLDPRT, Arm02.step.SLDPRT, ELENCO ARMATURE 01.SLDPRT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]
2019-11-15 Add gpio pin out voltage for seeing person
2019-11-16 Add holes for RPi, Arduino, and Power Circuit
    Also added CAD models for RPi, Arduino, Power Circuit, Battery, Servo, and RPi camera
    [Battery.SLDPRT, FeeTech FS5109M Metal Gear Servo Outer volume.SLDPRT, PoeSprint3Assem.SLDASM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]
2019-11-18 Modify code to use new Servo motors
    Commented or deleted unneeded code
2019-11-21 Update code to stop based on cameraPin
    Ignore stopPin since that connection was not working correctly. This code is working for movement (stopping and going at right times).
    [wheel_run.ino]
2019-12-03 Update CAD
    [Battery4.SLDPRT, FeeTech FS5109M Metal Gear Servo Outer volume4.SLDPRT, POEFinalSprint3cutsheet1.SLDDRW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]
2019-12-03 Comment reading frame lines (180 something in cv_person_detection.py)
2019-12-03 Increase time stopped while talking and get rid of pin 40 as stop moving
2019-12-03 Add battery indicator, untested
2019-12-03 Add variables to communicate to low battery to Raspi
2019-12-03 Lower amount of frames used to speed up person detection
2019-12-04 Move and resize holes
    [Battery.SLDPRT, PoeSprint3ChasisBotom.SLDPRT, PoeSprint4ChasisBotom.SLDPRT]
2019-12-04 Fix ServoMount hole distance
    [PoeSprint3ServoMount.SLDPRT]
2019-12-06 Add code to output low battery signal to Raspi
    Cleaned up comments and structure of code
2019-12-06 Final shit done!!!
    [POEFinalSprint3cutsheet2.SLDDRW, POEFinalSprint4cutsheet.SLDDRW, POESprint4CameraMountHead.SLDPRT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]
2019-12-06 Add battery voltage converting function
    Clean up code
2019-12-06 vinal cut sheet
2019-12-09 Add new Kicad schematic and move past Eagle schematic
    [SIK-DIP-board.brd, SIK-DIP-board.sch, The-Wanderer.sch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]
2019-12-09 Create a README for kicad files
2019-12-11 Fix schematic by replacing voltage divider with voltage converter
    [The-Wanderer.sch]
2019-12-13 Add voltage divider from battery to battInputPin
    [The-Wanderer.sch]
2019-12-16 Add voltage divider for battInputPin (actual)
    The commit before this was not successful
    [The-Wanderer.sch]

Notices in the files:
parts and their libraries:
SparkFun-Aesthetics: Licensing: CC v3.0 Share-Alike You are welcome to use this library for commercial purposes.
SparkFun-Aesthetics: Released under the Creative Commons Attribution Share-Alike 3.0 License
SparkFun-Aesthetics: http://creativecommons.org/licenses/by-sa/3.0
